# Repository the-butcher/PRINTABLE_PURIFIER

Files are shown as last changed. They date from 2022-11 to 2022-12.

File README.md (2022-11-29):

# PRINTABLE PURIFIER

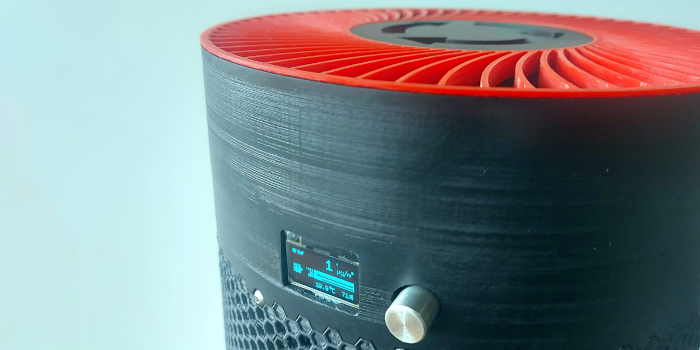
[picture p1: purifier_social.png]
PRINTABLE PURIFIER


An arduino powered air purifier, created mostly from 3D printed parts. Measured PM 2.5 dust readings and other parameters control the purifier's power output.

## [BUILDING INSTRUCTIONS](https://github.com/the-butcher/PRINTABLE_PURIFIER/tree/master/building_instructions/README.md)

Building instructions for the purifier. If you have a 3D-printer that can print 205x205mm you are good to go. I printed mine on an entry level Ancubic Mega S.

## [PART DETAILS](https://github.com/the-butcher/PRINTABLE_PURIFIER/tree/master/unit_purifier)

Complete set of parts provided as STL-Files.

## PICTURES

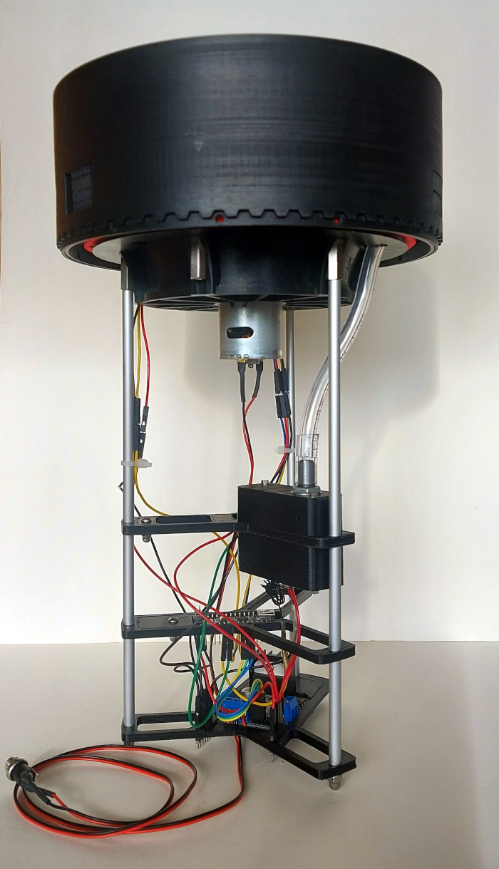
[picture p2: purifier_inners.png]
Purifier


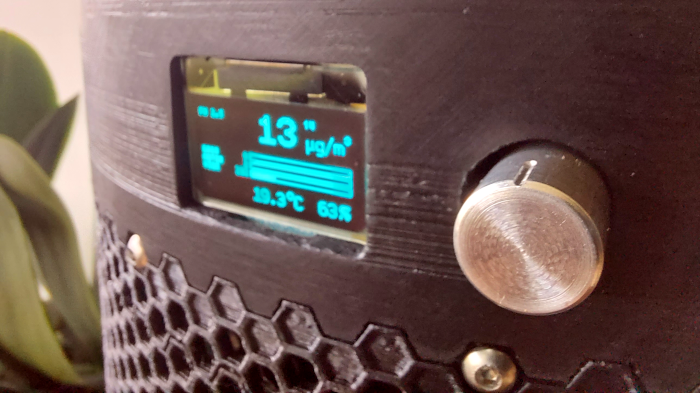
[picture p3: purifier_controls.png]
Purifier


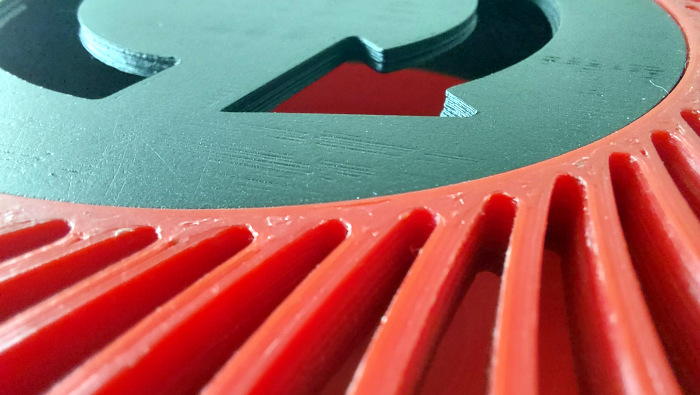
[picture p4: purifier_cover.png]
Purifier


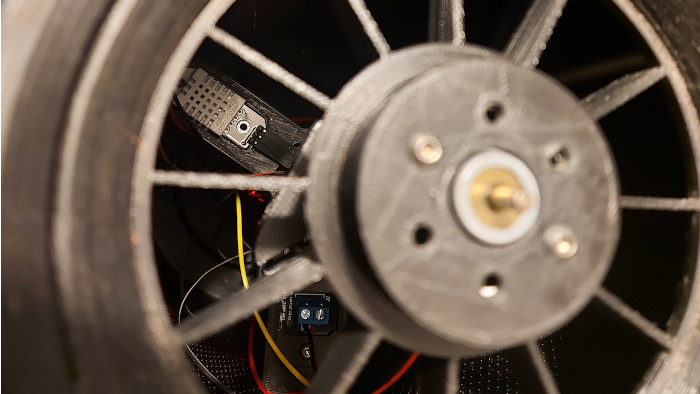
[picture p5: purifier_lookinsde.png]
Purifier


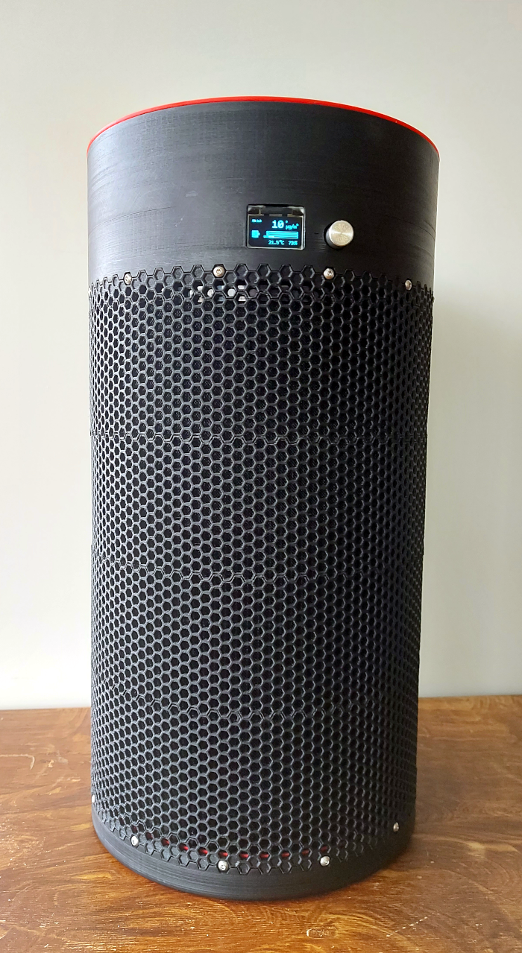
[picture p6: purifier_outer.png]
Purifier


To illustrate power of the device, i placed it upside down and let it run at full power. It actually starts to float on it's own airstream.

https://user-images.githubusercontent.com/84620977/204545599-40bb85f1-9fbe-4fc3-a840-4cbf5077d821.mov

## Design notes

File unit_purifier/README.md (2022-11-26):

# Printable Purifier (unit_purifier)

| | |
| --- | --- |
| Description | Assembly of all parts needed to build the purifier.  |
| Postprocessing | Please refer to postprocessing information of the respective parts. |
| Type | assembly |

---
## [Impeller (unit_impeller)](https://github.com/the-butcher/PRINTABLE_PURIFIER/tree/master/unit_purifier/unit_impeller)

| | |
| --- | --- |
| Description | The impeller is a challenging part to build. It requires precise axis alingnment of your printer and patience to find impeller balance. Please step into folder to find printable STL files.  Please step into folder to find more details and printable STL Files. |
| Type | assembly |

---
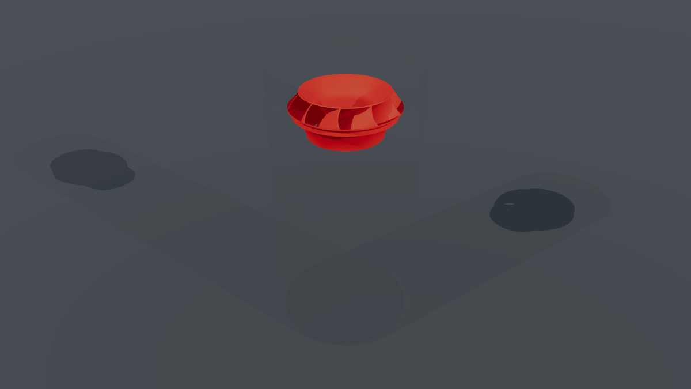
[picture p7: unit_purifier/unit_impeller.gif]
unit_impeller


---

## [Purifier inners (unit_inner)](https://github.com/the-butcher/PRINTABLE_PURIFIER/tree/master/unit_purifier/unit_inner)

| | |
| --- | --- |
| Description | The purifiers electronics were placed to inside the the filter. This part assembles motor, sensors, an arduino nano and the motor driver.  Please step into folder to find more details and printable STL Files. |
| Type | assembly |

---
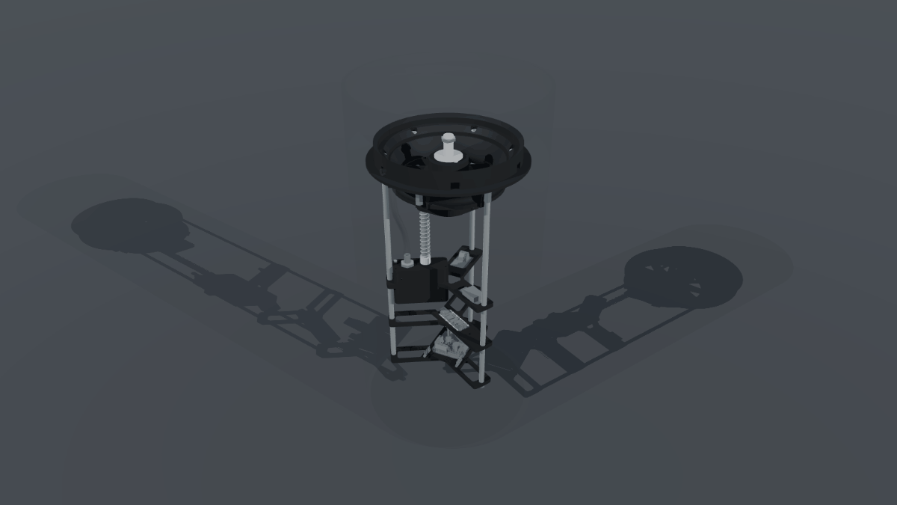
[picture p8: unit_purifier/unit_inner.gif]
unit_inner


---

## [Head (unit_head)](https://github.com/the-butcher/PRINTABLE_PURIFIER/tree/master/unit_purifier/unit_head)

| | |
| --- | --- |
| Description | The purifiers head with display and simple controls.  Please step into folder to find more details and printable STL Files. |
| Postprocessing | Glue "Lower head" to "Upper head", sand the combined part after glue has dried to remove glue remains, spray paint for a better finish. |
| Improvements | When sliding the head over the hub, it does not auto center on the hub. This can lead to not enough space between the impeller and the head. I inserted 6 strips cut from a plastic bottle between head and hub for even spacing. |
| Type | assembly |

---
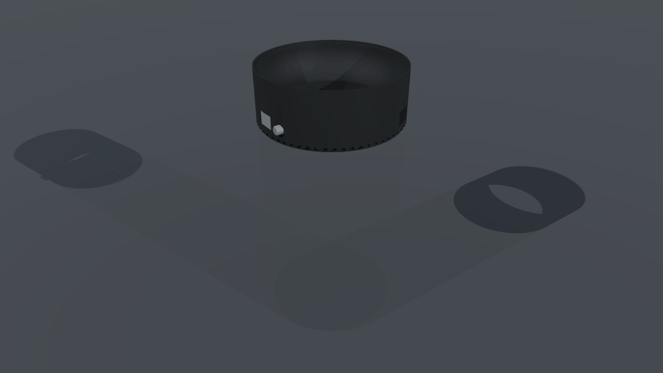
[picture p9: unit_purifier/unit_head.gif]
unit_head


---

## [Housing (unit_honeycomb)](https://github.com/the-butcher/PRINTABLE_PURIFIER/tree/master/unit_purifier/unit_honeycomb)

| | |
| --- | --- |
| Description | Housing around the Xiami Hepa filter.  Please step into folder to find more details and printable STL Files. |
| Type | assembly |

---
unit_honeycomb

---

## [Foot (unit_foot)](https://github.com/the-butcher/PRINTABLE_PURIFIER/tree/master/unit_purifier/unit_foot)

| | |
| --- | --- |
| Description | The purifiers foot.  Please step into folder to find more details and printable STL Files. |
| Type | assembly |

---
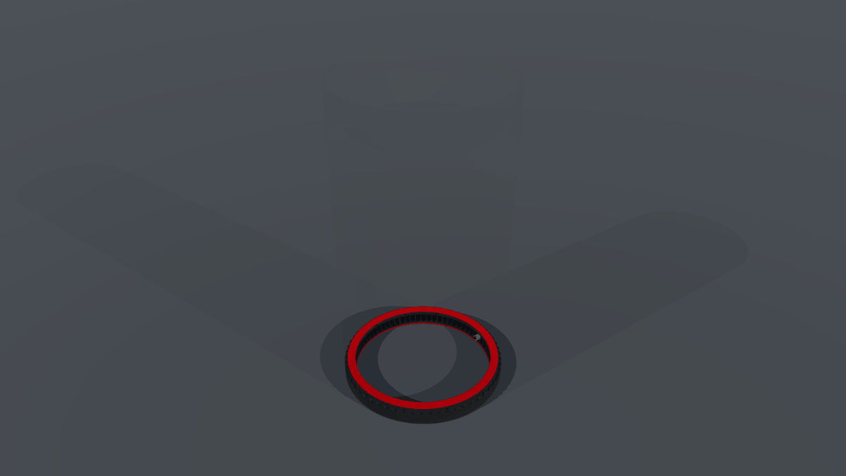
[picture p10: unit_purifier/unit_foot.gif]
unit_foot


---

## [Air outlet (unit_cover)](https://github.com/the-butcher/PRINTABLE_PURIFIER/tree/master/unit_purifier/unit_cover)

| | |
| --- | --- |
| Description | Air outlet assembly.  Please step into folder to find more details and printable STL Files. |
| Type | assembly |

---
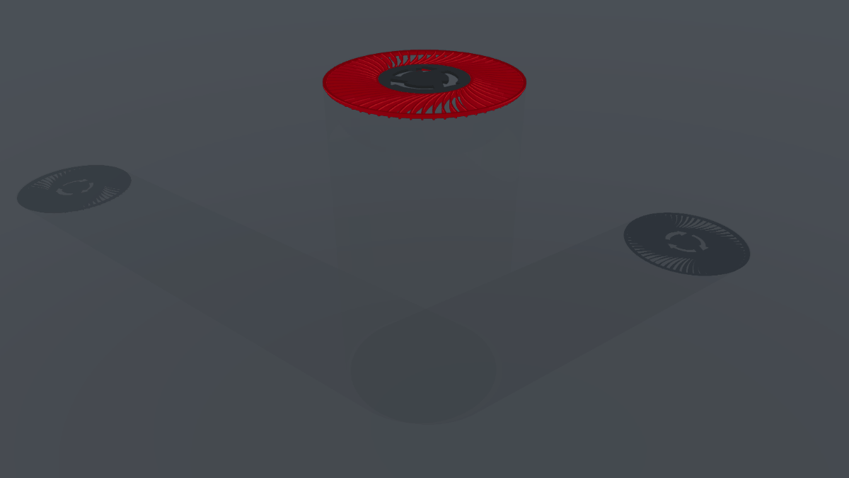
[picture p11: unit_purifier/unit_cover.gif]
unit_cover


---

## [Filter (unit_filter)](https://github.com/the-butcher/PRINTABLE_PURIFIER/tree/master/unit_purifier/unit_filter)

| | |
| --- | --- |
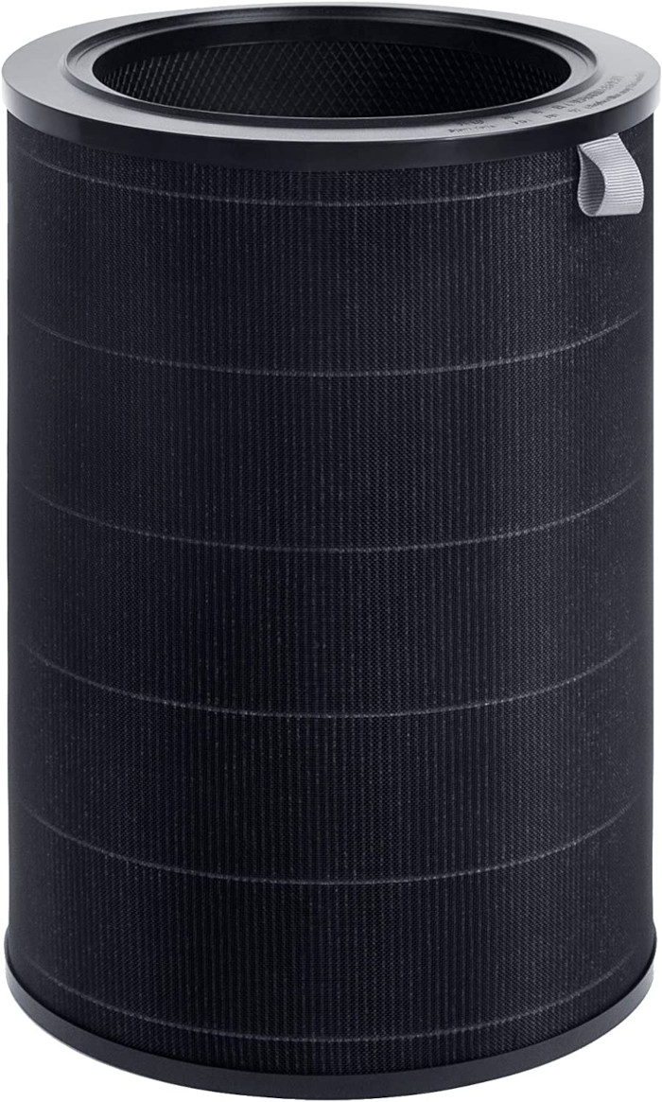
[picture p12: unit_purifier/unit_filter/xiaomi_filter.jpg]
Xiaomi Filter
| Description | The purifier is built around a Xiaomi Smartmi replacement filter. Please search for "Smartmi SMARTMI AIR PURIFIER Activated Carbon Filter, HEPA-H13" and make sure the filter found has the correct product dimensions of 20 x 20 x 29.3 cm.   Please step into folder to find more details and printable STL Files. |
| Type | assembly |

---
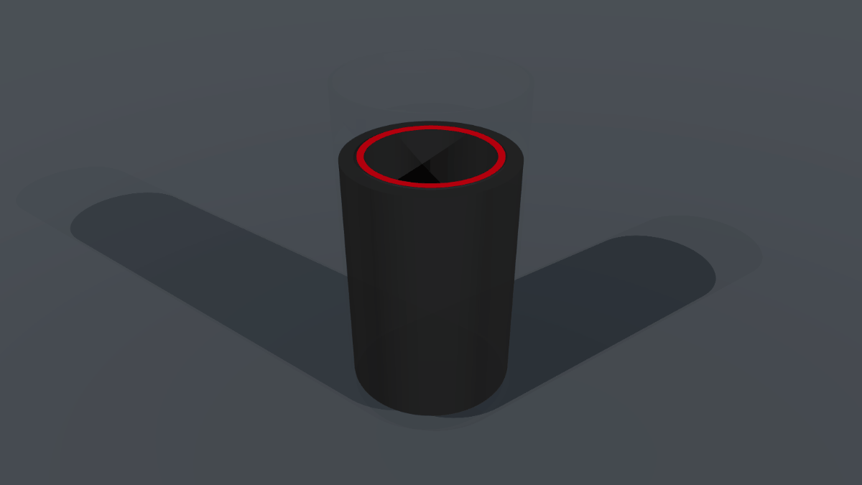
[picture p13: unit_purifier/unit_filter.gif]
unit_filter


---

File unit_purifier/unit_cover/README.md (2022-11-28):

# Air outlet (unit_cover)

| | |
| --- | --- |
| Description | Air outlet assembly.  |
| Type | assembly |

---
## Impeller cover (print_cover_1) &rarr; [STL File](https://github.com/the-butcher/PRINTABLE_PURIFIER/blob/master/unit_purifier/unit_cover/print_cover_1.stl)

| | |
| --- | --- |
| Description | This is the cover plate protecting both your fingers and the impeller.  |
| Improvements | In my build there was not enough space to let the cover slide in, so i had to file down ca. 1mm. I would suggest printing this part after completing the purifier head, so you already know how much space remains to fit it in. |
| Type | 3D print |

---
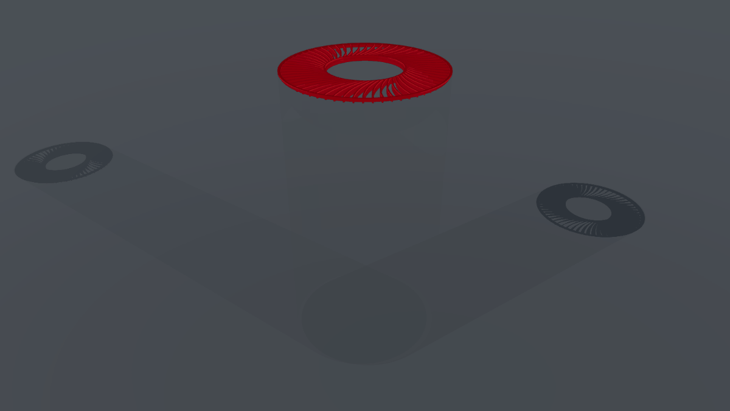
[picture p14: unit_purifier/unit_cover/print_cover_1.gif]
print_cover_1


---

## Customizeable cover (print_cover_2) &rarr; [STL File](https://github.com/the-butcher/PRINTABLE_PURIFIER/blob/master/unit_purifier/unit_cover/print_cover_2.stl)

| | |
| --- | --- |
| Description | This part is meant to be customizable by anyone building this device to give it a personal touch. When creating your own version, please ensure that there are no holes large enough to clear i.e. a child's hand.  |
| Postprocessing | Sand and spray paint for better finish. |
| Type | 3D print |

---
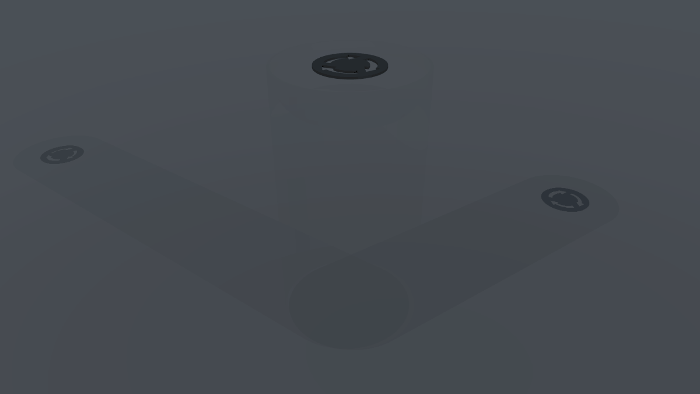
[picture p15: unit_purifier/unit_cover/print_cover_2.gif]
print_cover_2


---

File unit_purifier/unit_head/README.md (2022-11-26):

# Head (unit_head)

| | |
| --- | --- |
| Description | The purifiers head with display and simple controls.  |
| Postprocessing | Glue "Lower head" to "Upper head", sand the combined part after glue has dried to remove glue remains, spray paint for a better finish. |
| Improvements | When sliding the head over the hub, it does not auto center on the hub. This can lead to not enough space between the impeller and the head. I inserted 6 strips cut from a plastic bottle between head and hub for even spacing. |
| Type | assembly |

---
## Head connector (print_outer_connect) &rarr; [STL File](https://github.com/the-butcher/PRINTABLE_PURIFIER/blob/master/unit_purifier/unit_head/print_outer_connect.stl)

| | |
| --- | --- |
| Description | This part connects the outer and inner parts of the head.  |
| Postprocessing | With a 3mm drill widen the 12 holes. This will make it easier to insert the M3 screws when assembling the purifier. |
| Type | 3D print |

---
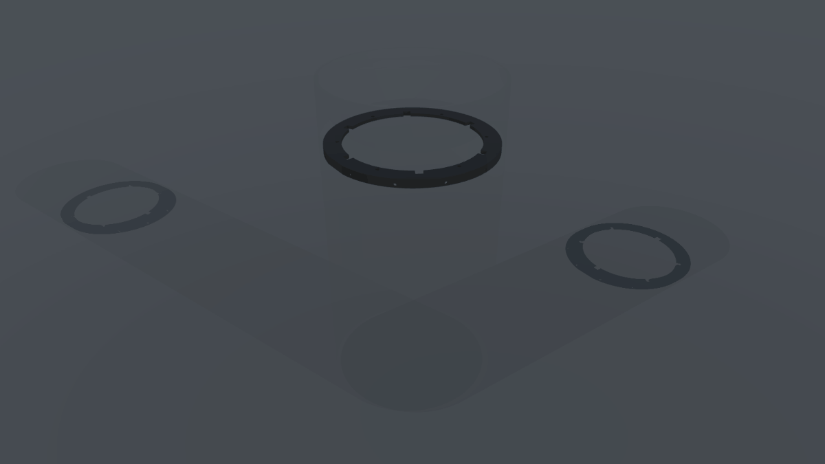
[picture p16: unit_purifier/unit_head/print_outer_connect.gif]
print_outer_connect


---

## Lower head (print_outer_controls) &rarr; [STL File](https://github.com/the-butcher/PRINTABLE_PURIFIER/blob/master/unit_purifier/unit_head/print_outer_controls.stl)

| | |
| --- | --- |
| Description | The lower part of the outfacing head. This part holds the OLED display and the potentiometer that controls the power setting.  |
| Postprocessing | User pliers to remove supports. Clean up openings for display and potentiometer so these fit properly. |
| Improvements | In my build the pins on the outside of the OLED display were portruding too far to fit the display. I had to file away some material from the display opening. |
| Type | 3D print |

---
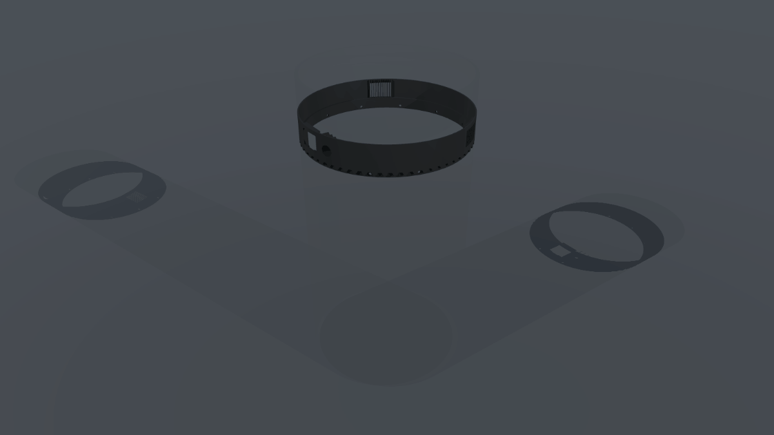
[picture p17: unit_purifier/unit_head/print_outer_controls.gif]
print_outer_controls


---

## Inner head (print_outer_outlet) &rarr; [STL File](https://github.com/the-butcher/PRINTABLE_PURIFIER/blob/master/unit_purifier/unit_head/print_outer_outlet.stl)

| | |
| --- | --- |
| Description | The infacing part of the head.  |
| Postprocessing | Use a 4mm drill to open the screwholes. Use a 4mm screw to pull M4 nuts into the respective openings. The nuts should have a tight fit and not come out, once seated.
Sand and spray for a better finish. |
| Type | 3D print |

---
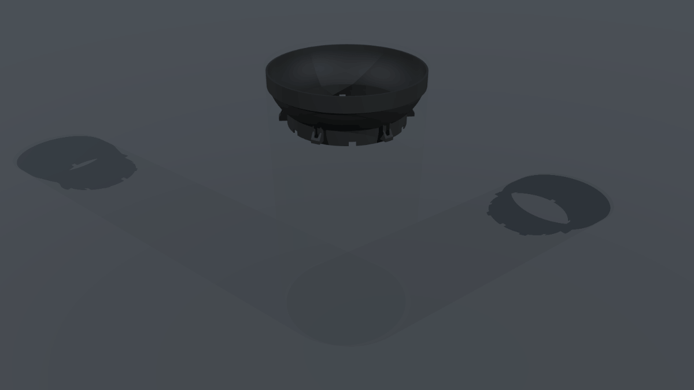
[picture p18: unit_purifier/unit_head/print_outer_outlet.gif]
print_outer_outlet


---

## Upper head (print_outer_ring) &rarr; [STL File](https://github.com/the-butcher/PRINTABLE_PURIFIER/blob/master/unit_purifier/unit_head/print_outer_ring.stl)

| | |
| --- | --- |
| Description | The upper part of the outfacing head.  |
| Type | 3D print |

---
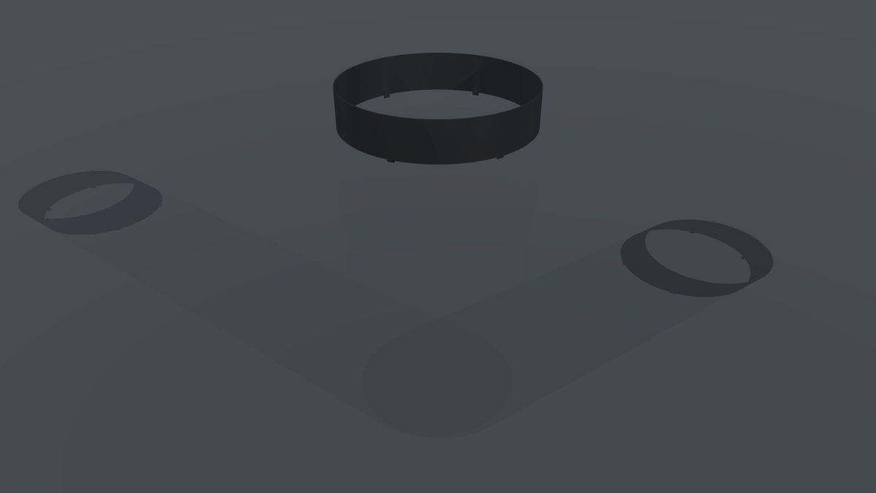
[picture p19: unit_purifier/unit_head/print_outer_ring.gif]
print_outer_ring


---

## Display (display_ssd1306)

| | |
| --- | --- |
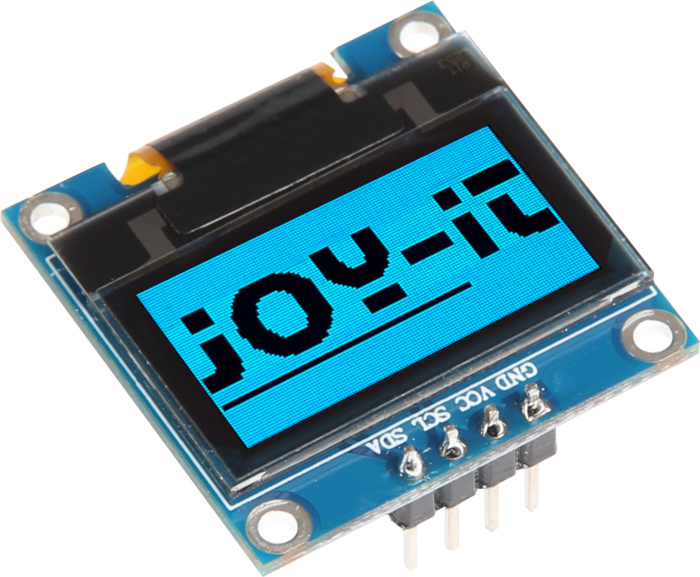
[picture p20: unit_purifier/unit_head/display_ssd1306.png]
SD1306
| Description | Type SSD1306 display. Search the internet for SD1306 display.   |
| Type | electronic |

---

## Potentiometer (poti_smc10h04103)

| | |
| --- | --- |
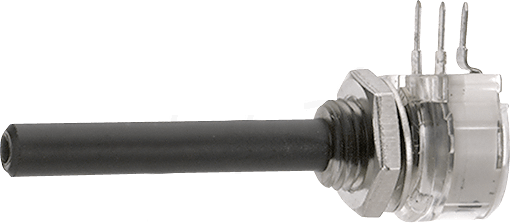
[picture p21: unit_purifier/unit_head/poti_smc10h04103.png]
smc10h04103
| Description | Ptentiometer 10 kOhm. Search the internet for poti_smc10h04103 potentiometer.   |
| Type | electronic |

---

## M4 nut (hardware_nut_m4)

| | |
| --- | --- |
| Description | M4 nut, 6 pieces.  |
| Type | hardware |

---

## M4 screw (hardware_allen_m4_14mm)

| | |
| --- | --- |
| Description | M4 allen screw, 14mm long. 6 pieces.  |
| Type | hardware |

---

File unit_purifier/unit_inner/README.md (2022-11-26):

# Purifier inners (unit_inner)

| | |
| --- | --- |
| Description | The purifiers electronics were placed to inside the the filter. This part assembles motor, sensors, an arduino nano and the motor driver.  |
| Type | assembly |

---
## [Hub (unit_hub)](https://github.com/the-butcher/PRINTABLE_PURIFIER/tree/master/unit_purifier/unit_inner/unit_hub)

| | |
| --- | --- |
| Description | The hub holds the motor and acts a guide for the air as it exits the filter.  Please step into folder to find more details and printable STL Files. |
| Type | assembly |

---
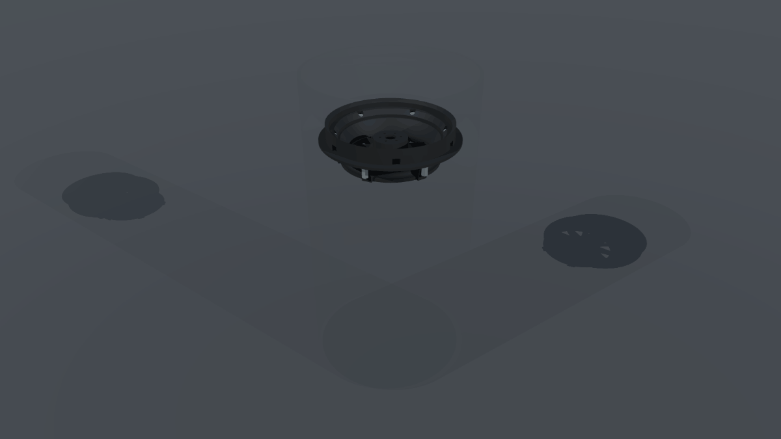
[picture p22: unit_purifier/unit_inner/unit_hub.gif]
unit_hub


---

## [Motor assembly (unit_motor)](https://github.com/the-butcher/PRINTABLE_PURIFIER/tree/master/unit_purifier/unit_inner/unit_motor)

| | |
| --- | --- |
| Description | The motor assembly contains the motor, the connecting part to the impeller and a connection to the vibration sensor.  Please step into folder to find more details and printable STL Files. |
| Type | assembly |

---
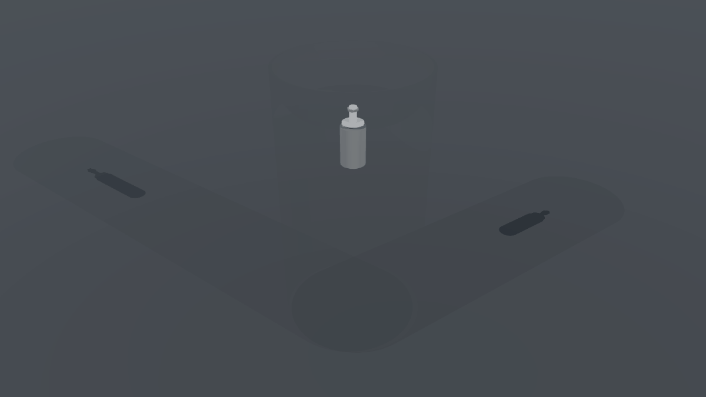
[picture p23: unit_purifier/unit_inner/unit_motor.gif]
unit_motor


---

## [Arduino Nano (unit_nano)](https://github.com/the-butcher/PRINTABLE_PURIFIER/tree/master/unit_purifier/unit_inner/unit_nano)

| | |
| --- | --- |
| Description | The plate holding the Arduino Nano.  Please step into folder to find more details and printable STL Files. |
| Type | assembly |

---
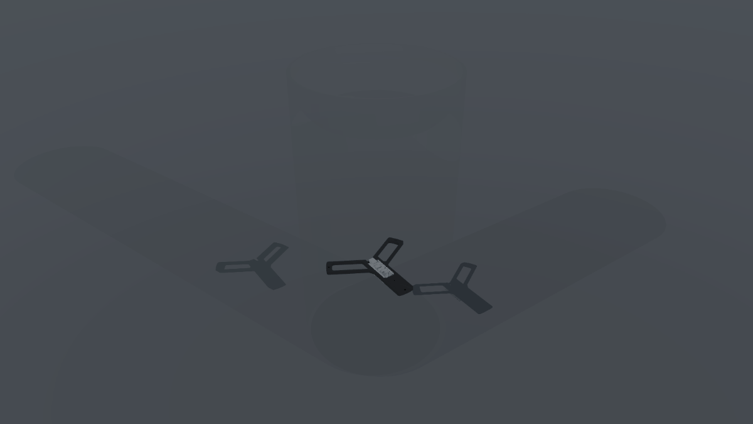
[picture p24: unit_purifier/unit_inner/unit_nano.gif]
unit_nano


---

## [Motor driver (unit_power)](https://github.com/the-butcher/PRINTABLE_PURIFIER/tree/master/unit_purifier/unit_inner/unit_power)

| | |
| --- | --- |
| Description | The plate holding the L298N motor driver.  Please step into folder to find more details and printable STL Files. |
| Type | assembly |

---
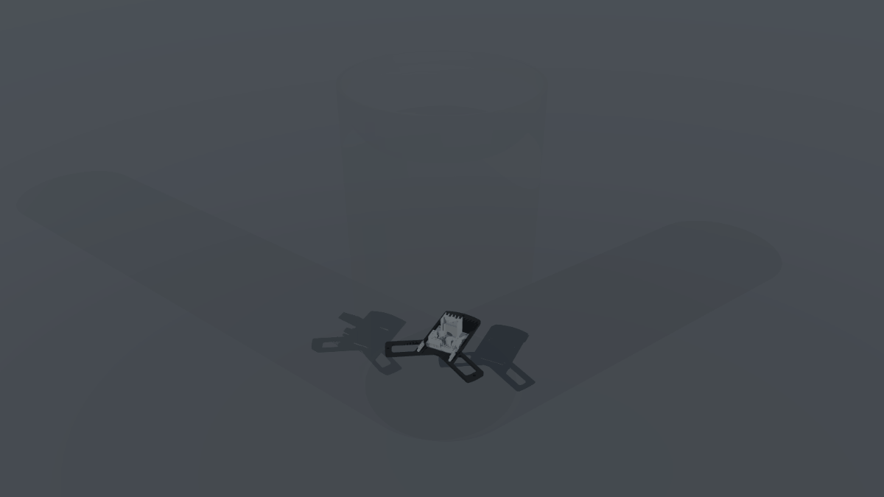
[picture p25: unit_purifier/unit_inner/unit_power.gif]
unit_power


---

## [Sensors (unit_sensors)](https://github.com/the-butcher/PRINTABLE_PURIFIER/tree/master/unit_purifier/unit_inner/unit_sensors)

| | |
| --- | --- |
| Description | The plate holding the sensors.  Please step into folder to find more details and printable STL Files. |
| Type | assembly |

---
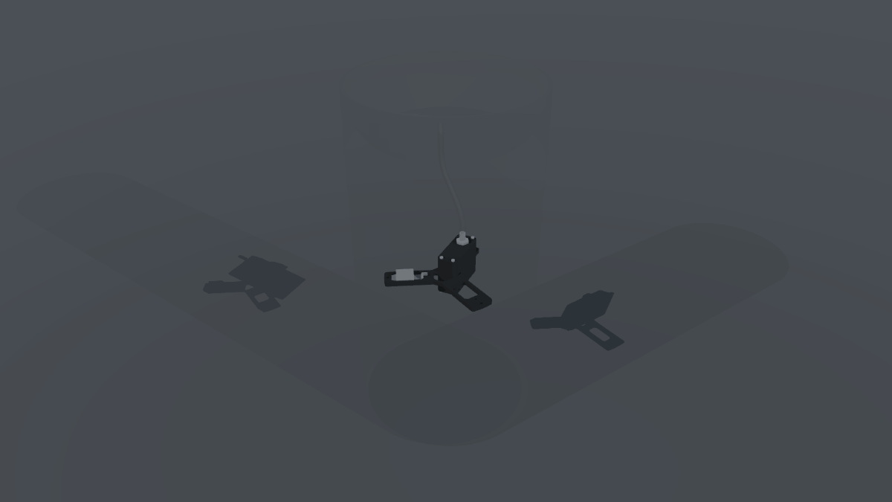
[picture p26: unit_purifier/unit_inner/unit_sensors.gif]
unit_sensors


---

## [Screws (unit_screws)](https://github.com/the-butcher/PRINTABLE_PURIFIER/tree/master/unit_purifier/unit_inner/unit_screws)

| | |
| --- | --- |
| Description | All hardware needed to assemble the purifier inner parts.  Please step into folder to find more details and printable STL Files. |
| Type | assembly |

---
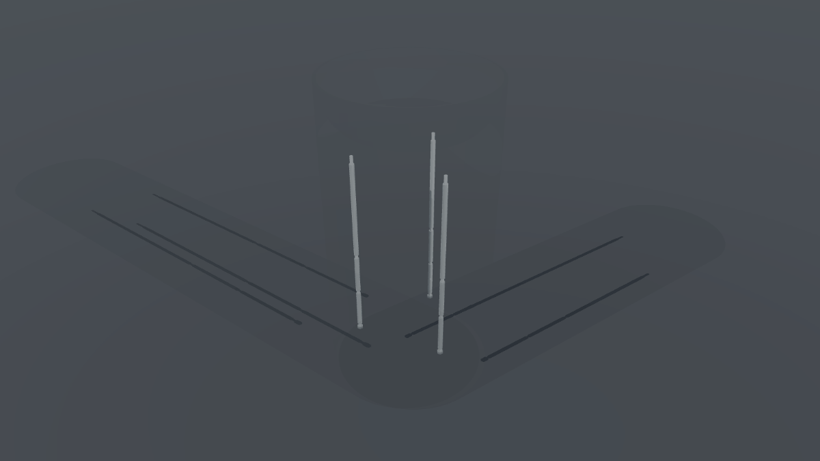
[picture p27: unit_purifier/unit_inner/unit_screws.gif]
unit_screws


---

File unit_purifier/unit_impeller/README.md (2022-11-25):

# Impeller (unit_impeller)

| | |
| --- | --- |
| Description | The impeller is a challenging part to build. It requires precise axis alingnment of your printer and patience to find impeller balance. Please step into folder to find printable STL files.  |
| Type | assembly |

---
## Lower impeller (print_impeller_1) &rarr; [STL File](https://github.com/the-butcher/PRINTABLE_PURIFIER/blob/master/unit_purifier/unit_impeller/print_impeller_1.stl)

| | |
| --- | --- |
| Description | The lower part of the impeller.  |
| Type | 3D print |

---
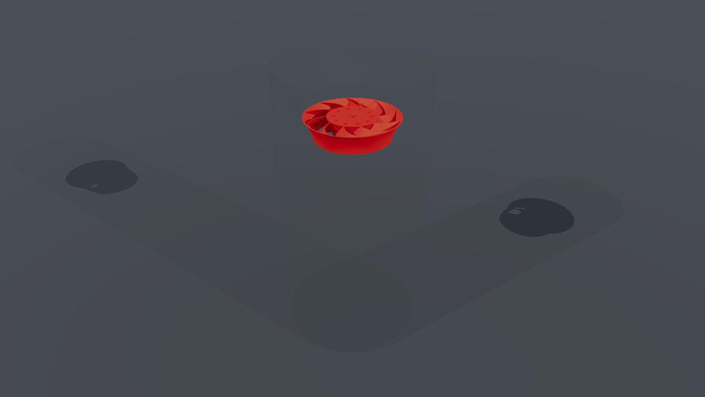
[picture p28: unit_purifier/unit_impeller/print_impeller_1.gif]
print_impeller_1


---

## Upper Impeller (print_impeller_2) &rarr; [STL File](https://github.com/the-butcher/PRINTABLE_PURIFIER/blob/master/unit_purifier/unit_impeller/print_impeller_2.stl)

| | |
| --- | --- |
| Description | The upper part of the impeller.  |
| Type | 3D print |

---
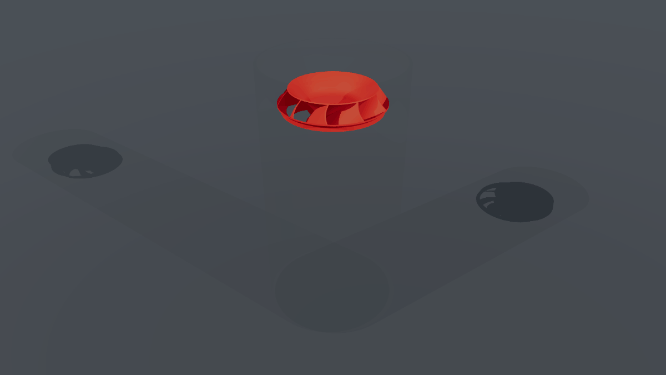
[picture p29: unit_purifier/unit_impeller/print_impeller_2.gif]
print_impeller_2


---

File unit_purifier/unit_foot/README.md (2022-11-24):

# Foot (unit_foot)

| | |
| --- | --- |
| Description | The purifiers foot.  |
| Type | assembly |

---
## Foot (print_outer_foot) &rarr; [STL File](https://github.com/the-butcher/PRINTABLE_PURIFIER/blob/master/unit_purifier/unit_foot/print_outer_foot.stl)

| | |
| --- | --- |
| Description | The purifiers foot  |
| Postprocessing | User pliers to remove supports from plug opening and cut M8x1 fine thread to fit the power plug. Sand and spray paint for a better finish. Cut rings of foam rubber for both bottom and top of the foot, then glue foam rubber to foot. |
| Type | 3D print |

---
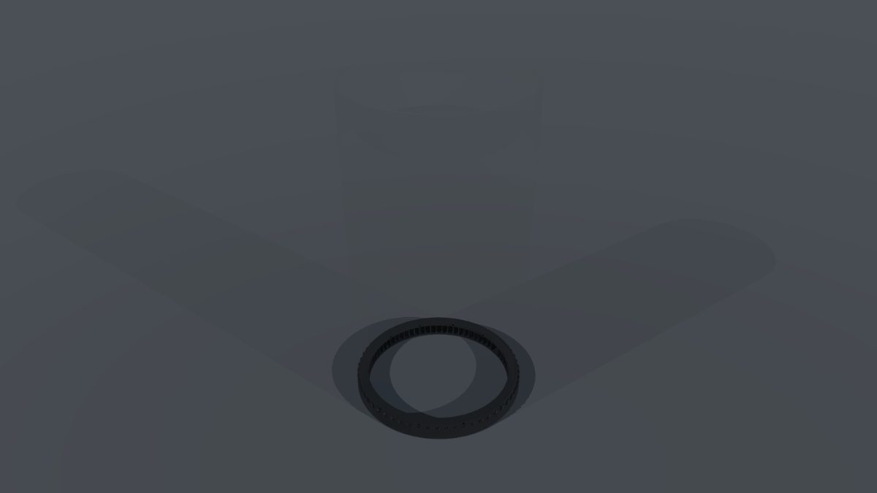
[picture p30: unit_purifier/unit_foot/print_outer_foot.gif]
print_outer_foot


---

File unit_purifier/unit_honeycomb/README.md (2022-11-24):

# Housing (unit_honeycomb)

| | |
| --- | --- |
| Description | Housing around the Xiami Hepa filter.  |
| Type | assembly |

---
## Lower housing (print_honeycomb_1) &rarr; [STL File](https://github.com/the-butcher/PRINTABLE_PURIFIER/blob/master/unit_purifier/unit_honeycomb/print_honeycomb_1.stl)

| | |
| --- | --- |
| Description | The lower border of the purifier housing.  |
| Postprocessing | User pliers to remove supports. Carefully widen the 1mm holes to 2mm first, then to 3mm. File and sand the upper hexagon border so it properly fits the upper housing part. I used rough sand paper wrapped around an allen key to file multiple hexagon side at once. |
| Type | 3D print |

---
print_honeycomb_1

---

## Center housing (print_honeycomb_2) &rarr; [STL File](https://github.com/the-butcher/PRINTABLE_PURIFIER/blob/master/unit_purifier/unit_honeycomb/print_honeycomb_2.stl)

| | |
| --- | --- |
| Description | The center piece of the purifier housing. Attention: 4 pieces needed to get the full housing.  |
| Postprocessing | User pliers to remove supports. File and sand upper and lower hexagon border so it properly fits the housing parts above and below. I used rough sand paper wrapped around an allen key to file multiple hexagon side at once. |
| Type | 3D print |

---
print_honeycomb_2

---

## Upper housing (print_honeycomb_3) &rarr; [STL File](https://github.com/the-butcher/PRINTABLE_PURIFIER/blob/master/unit_purifier/unit_honeycomb/print_honeycomb_3.stl)

| | |
| --- | --- |
| Description | The upper border of the purifier housing.  |
| Postprocessing | User pliers to remove supports. Carefully widen the 1mm holes to 2mm first, then to 3mm. File and sand the lower hexagon border so it properly fits the housing part below. I used rough sand paper wrapped around an allen key to file multiple hexagon side at once. |
| Type | 3D print |

---
print_honeycomb_3

---

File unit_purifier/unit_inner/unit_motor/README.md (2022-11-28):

# Motor assembly (unit_motor)

| | |
| --- | --- |
| Description | The motor assembly contains the motor, the connecting part to the impeller and a connection to the vibration sensor.  |
| Type | assembly |

---
## Impeller mount (lathe_motor_connect) &rarr; [STL File](https://github.com/the-butcher/PRINTABLE_PURIFIER/blob/master/unit_purifier/unit_inner/unit_motor/lathe_motor_connect.stl)

| | |
| --- | --- |
| Description | This part is used to connect the impeller parts and to fix the impeller to the 3.2mm axle of the motor. In my build i made the part from a leftover piece of 30mm POM  |
| Postprocessing | Cut a M10x1 thread on the 10mm end of the part, use a M10x1 nut for connecting the impeller parts. Have a 3mm hole in the part for a firm fit when pushing the part onto the motor axle. |
| Type | lathe |

---

## Motor (motor_555_1)

| | |
| --- | --- |
| Description | Type 555-1 motor. Search the internet for 555-1 motor.   |
| Type | electronic |

---

## M3 lens head (hardware_flat_allen_m3)

| | |
| --- | --- |
| Description | M3 lens head allen screw, 10mm long, 2 pieces.  |
| Type | hardware |

---

## M10x1 nut (hardware_nut_m10)

| | |
| --- | --- |
| Description | M10x1 fine threaded nut.  |
| Type | hardware |

---

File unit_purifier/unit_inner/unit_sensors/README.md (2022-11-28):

# Sensors (unit_sensors)

| | |
| --- | --- |
| Description | The plate holding the sensors.  |
| Type | assembly |

---
## Sensor Plate (print_holder_sensors_1) &rarr; [STL File](https://github.com/the-butcher/PRINTABLE_PURIFIER/blob/master/unit_purifier/unit_inner/unit_sensors/print_holder_sensors_1.stl)

| | |
| --- | --- |
| Description | The main plate holding Dust, Temperature and Vibration Sensor.  |
| Type | 3D print |

---
print_holder_sensors_1

---

## Sensor holder (print_holder_sensors_2) &rarr; [STL File](https://github.com/the-butcher/PRINTABLE_PURIFIER/blob/master/unit_purifier/unit_inner/unit_sensors/print_holder_sensors_2.stl)

| | |
| --- | --- |
| Description | Holding plate for the Vibration sensor.  |
| Type | 3D print |

---
print_holder_sensors_2

---

## Sensor housing (print_holder_sensors_3) &rarr; [STL File](https://github.com/the-butcher/PRINTABLE_PURIFIER/blob/master/unit_purifier/unit_inner/unit_sensors/print_holder_sensors_3.stl)

| | |
| --- | --- |
| Description | Upper housing of the dust sensor.  |
| Type | 3D print |

---
print_holder_sensors_3

---

## Sensor housing (print_holder_sensors_4) &rarr; [STL File](https://github.com/the-butcher/PRINTABLE_PURIFIER/blob/master/unit_purifier/unit_inner/unit_sensors/print_holder_sensors_4.stl)

| | |
| --- | --- |
| Description | Lower housing of the dust sensor.  |
| Type | 3D print |

---
print_holder_sensors_4

---

## Dust sensor (sensor_pd_m4)

| | |
| --- | --- |
| Description | The dust sensor is the input to the purifiers power level, together with the potentiometer setting. I used a sensor that i already had: PD-M4 [PM-D4](http://www.csfan.co.kr/bbs/board.php?bo_table=products1&wr_id=15&ckattempt=2). This sensor appears not to be available in retail, therefore another sensor may have to be used, thus requiring changes to the sensor plate and to the sensor housing parts!  |
| Type | electronic |

---

## Temperature and humidity sensor (sensor_dht22)

| | |
| --- | --- |
| Description | For added value a temperature and humidity sensor was included. This sensor provided information only and does not contribute to the purifiers power setting. Sensor used: DHT22 [DHT22](https://joy-it.net/en/products/SEN-DHT22)  |
| Type | electronic |

---

## M2 rod (hardware_rod_m2_49)

| | |
| --- | --- |
| Description | M2 rod, 49mm long, 4 pieces.  |
| Type | hardware |

---

## M12 nut (hardware_nut_m2)

| | |
| --- | --- |
| Description | M2 nut. 8 pieces.  |
| Type | hardware |

---

## M10x1 nut (hardware_nut_m10)

| | |
| --- | --- |
| Description | M10x1 fine threaded nut. 2 pieces.  |
| Type | hardware |

---

## Cleartube (hardware_cleartube_10)

| | |
| --- | --- |
| Description | Cleartube, 10mm diameter, ~140mm long.  |
| Type | hardware |

---

## Cleartube (hardware_cleartube_12)

| | |
| --- | --- |
| Description | Cleartube, 12mm diameter, 20mm long.  |
| Type | hardware |

---

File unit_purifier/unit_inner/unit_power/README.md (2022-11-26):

# Motor driver (unit_power)

| | |
| --- | --- |
| Description | The plate holding the L298N motor driver.  |
| Type | assembly |

---
## Driver Plate (print_holder_power_1) &rarr; [STL File](https://github.com/the-butcher/PRINTABLE_PURIFIER/blob/master/unit_purifier/unit_inner/unit_power/print_holder_power_1.stl)

| | |
| --- | --- |
| Description | The main plate holding the motor driver.  |
| Type | 3D print |

---
print_holder_power_1

---

## Driver holder (print_holder_power_2) &rarr; [STL File](https://github.com/the-butcher/PRINTABLE_PURIFIER/blob/master/unit_purifier/unit_inner/unit_power/print_holder_power_2.stl)

| | |
| --- | --- |
| Description | Holding plate for the motor driver.  |
| Type | 3D print |

---
print_holder_power_2

---

## Motor driver (driver_l298n)

| | |
| --- | --- |
| Description | The L298N driver regulating motor power. L298N  |
| Type | electronic |

---

## Power plug (driver_plug_5521)

| | |
| --- | --- |
| Description | Power plug 5.5x2.1 mm. Power Plug  |
| Type | electronic |

---

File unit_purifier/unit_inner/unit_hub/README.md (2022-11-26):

# Hub (unit hub)

| | |
| --- | --- |
| Description | The hub holds the motor and acts a guide for the air as it exits the filter.  |
| Type | assembly |

---
## Lower hub (print_hub_1) &rarr; [STL File](https://github.com/the-butcher/PRINTABLE_PURIFIER/blob/master/unit_purifier/unit_inner/unit_hub/print_hub_1.stl)

| | |
| --- | --- |
| Description | The lower part of the impeller hub.  |
| Postprocessing | Remove the supports. Smoothen air outlet a bit to improve air flow and reduce noise. |
| Improvements | Create supports that are easier to remove, especially for the motor opening. Maybe make the motor opening a little larger, i had to do some sanding in my build before the motor could be fitted. |
| Type | 3D print |

---
print_hub_1

---

## Upper hub. (print_hub_2) &rarr; [STL File](https://github.com/the-butcher/PRINTABLE_PURIFIER/blob/master/unit_purifier/unit_inner/unit_hub/print_hub_2.stl)

| | |
| --- | --- |
| Description | The upper part of the impeller hub.  |
| Postprocessing | Remove support from the opening where the dust sensors tub passed through. Later place electric tape over the unused outlet openings. |
| Type | 3D print |

---
print_hub_2

---

## M4 long nut (hardware_nut_m4_20mm)

| | |
| --- | --- |
| Description | M4 nut, 20mm long, 6 pieces.  |
| Type | hardware |

---

## M4 screw (hardware_allen_m4_14mm)

| | |
| --- | --- |
| Description | M4 allen screw, 14mm long. 6 pieces.  |
| Type | hardware |

---

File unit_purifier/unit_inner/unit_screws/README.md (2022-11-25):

# Screws (unit_screws)

| | |
| --- | --- |
| Description | All hardware needed to assemble the purifier inner parts.  |
| Type | assembly |

---
## M4 rod (hardware_rod_m4_253)

| | |
| --- | --- |
| Description | M4 rod, 253mm long, 3 pieces.  |
| Type | hardware |

---

## Aluminum Tube (hardware_tube_6_1_125)

| | |
| --- | --- |
| Description | Aluminum Tube 6x1mm 125mm long, 3 pieces.  |
| Type | hardware |

---

## Aluminum Tube (hardware_tube_6_1_50)

| | |
| --- | --- |
| Description | Aluminum Tube 6x1mm 50mm long, 6 pieces.  |
| Type | hardware |

---

## M4 nut (hardware_nut_m4)

| | |
| --- | --- |
| Description | M4 nut, 3 pieces.  |
| Type | hardware |

---

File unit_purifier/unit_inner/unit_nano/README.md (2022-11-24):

# Arduino Nano (unit_nano)

| | |
| --- | --- |
| Description | The plate holding the Arduino Nano.  |
| Type | assembly |

---
## Controller Plate (print_holder_nano_1) &rarr; [STL File](https://github.com/the-butcher/PRINTABLE_PURIFIER/blob/master/unit_purifier/unit_inner/unit_nano/print_holder_nano_1.stl)

| | |
| --- | --- |
| Description | The main plate holding the Arduino Nano.  |
| Type | 3D print |

---
print_holder_nano_1

---

## Controller holder (print_holder_nano_2) &rarr; [STL File](https://github.com/the-butcher/PRINTABLE_PURIFIER/blob/master/unit_purifier/unit_inner/unit_nano/print_holder_nano_2.stl)

| | |
| --- | --- |
| Description | Holding plate for the Arduino Nano.  |
| Type | 3D print |

---
print_holder_nano_2

---

## Arduino Nano (arduino_nano)

| | |
| --- | --- |
| Description | An original Arduino Nano or a Nano clone.  Arduino Nano  |
| Type | electronic |

---

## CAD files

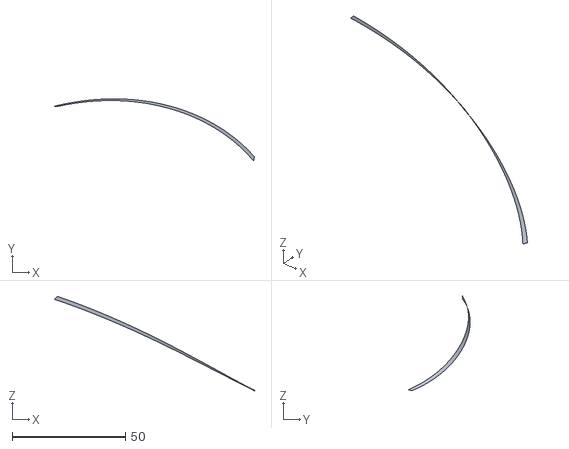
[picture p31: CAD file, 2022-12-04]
misc/imp_test_draw_curve2_wing_sec_b.stl
88.3 x 27.5 x 41.6

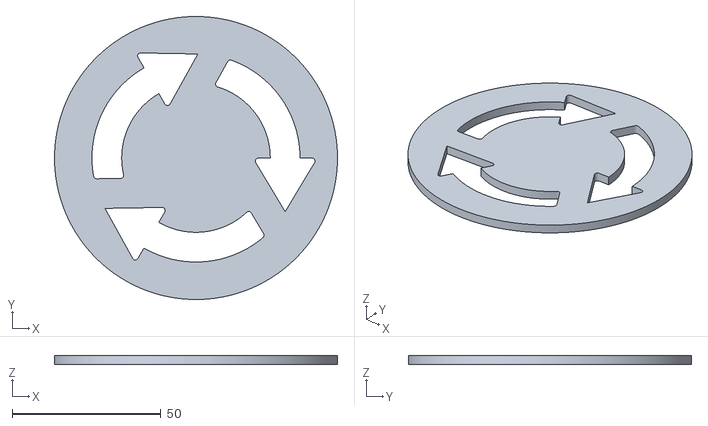
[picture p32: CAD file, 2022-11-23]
unit_purifier/unit_cover/print_cover_2.stl
95.2 x 95.2 x 3.00

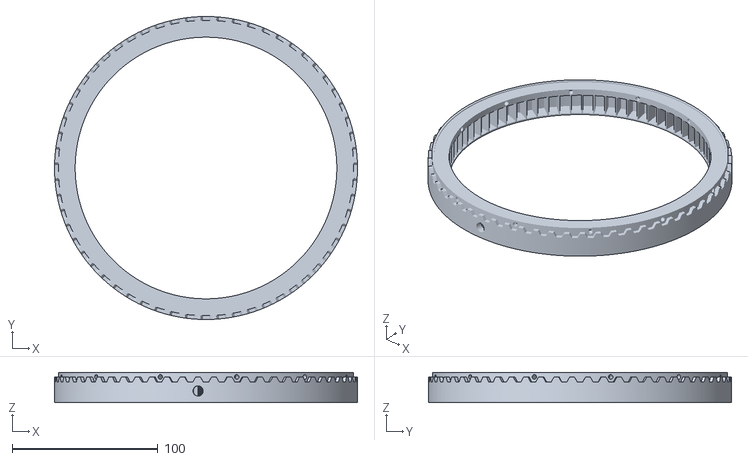
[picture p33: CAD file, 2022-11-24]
unit_purifier/unit_foot/print_outer_foot.stl
208.0 x 208.0 x 20.8

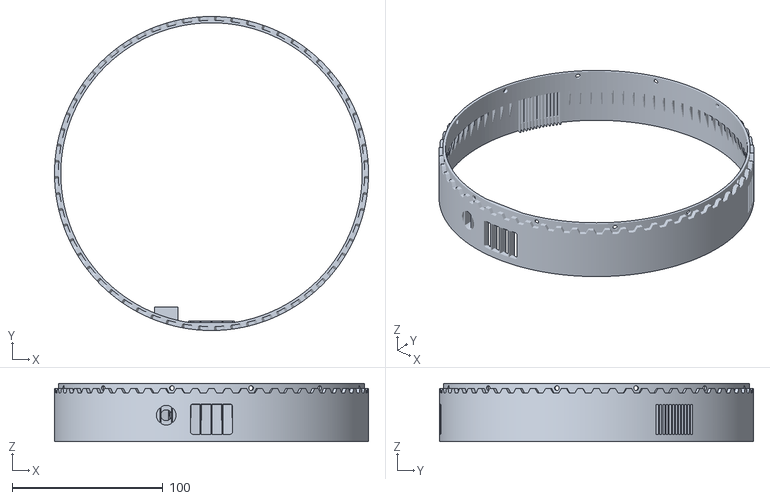
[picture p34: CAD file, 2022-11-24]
unit_purifier/unit_head/print_outer_controls.stl
208.0 x 208.0 x 38.6

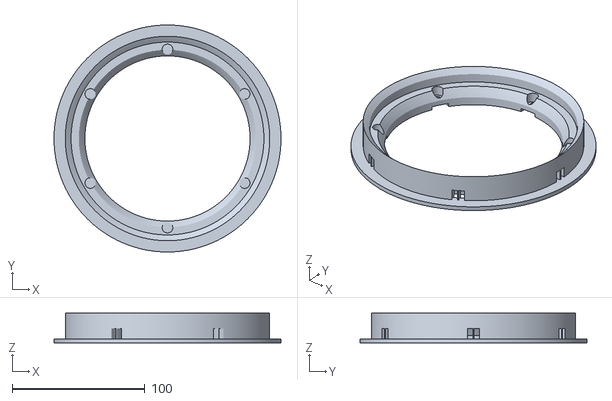
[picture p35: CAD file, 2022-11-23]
unit_purifier/unit_inner/unit_hub/print_hub_2.stl
170.7 x 170.7 x 22.3

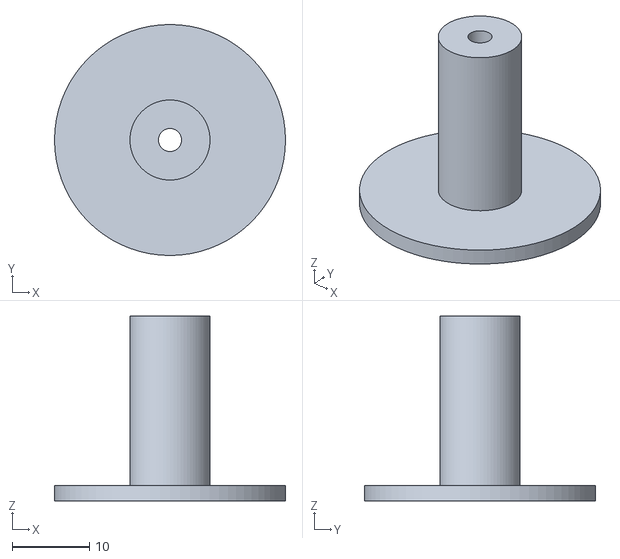
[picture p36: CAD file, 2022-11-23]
unit_purifier/unit_inner/unit_motor/lathe_motor_connect.stl
30.0 x 30.0 x 24.0

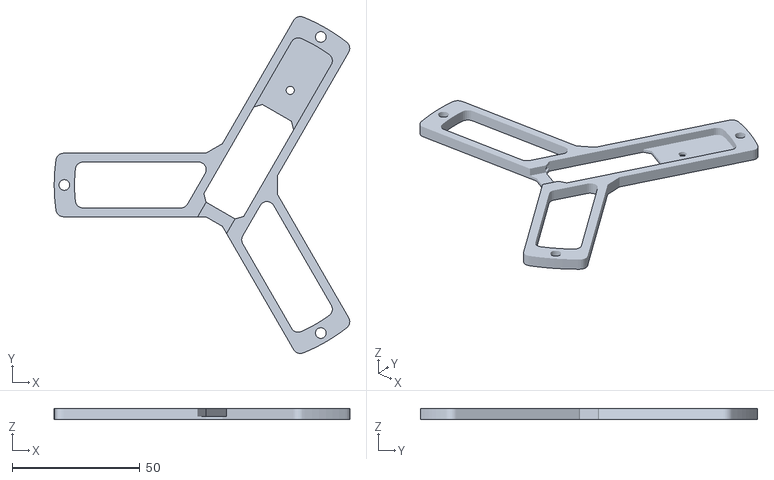
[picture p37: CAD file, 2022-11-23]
unit_purifier/unit_inner/unit_nano/print_holder_nano_1.stl
115.9 x 132.1 x 4.38

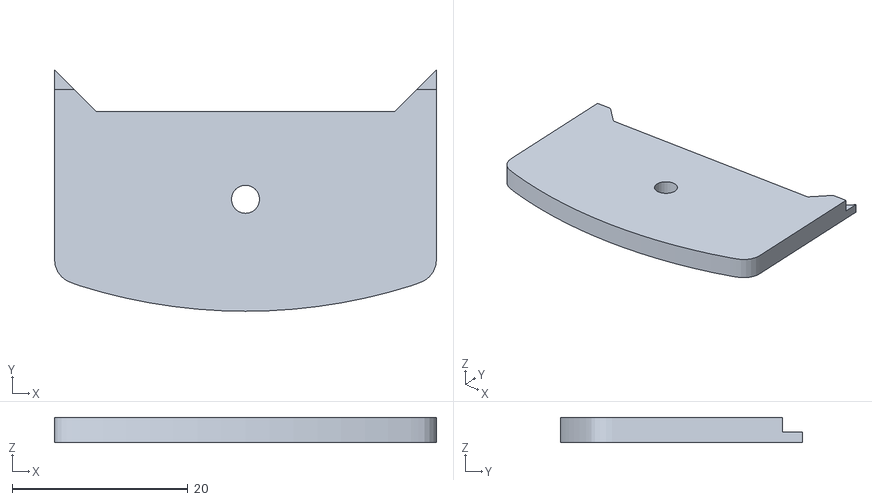
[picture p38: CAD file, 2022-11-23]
unit_purifier/unit_inner/unit_power/print_holder_power_2.stl
43.5 x 27.5 x 2.90

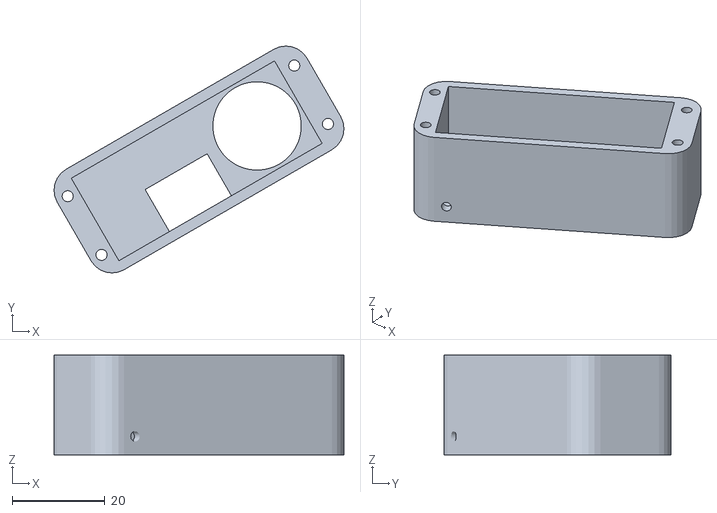
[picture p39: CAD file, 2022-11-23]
unit_purifier/unit_inner/unit_sensors/print_holder_sensors_4.stl
62.4 x 48.8 x 21.4

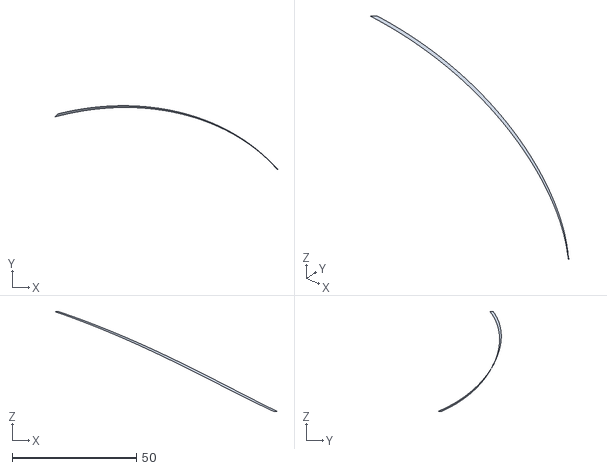
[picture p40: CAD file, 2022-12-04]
misc/imp_test_draw_curve2_wing_sec_c.stl
89.8 x 25.6 x 40.3

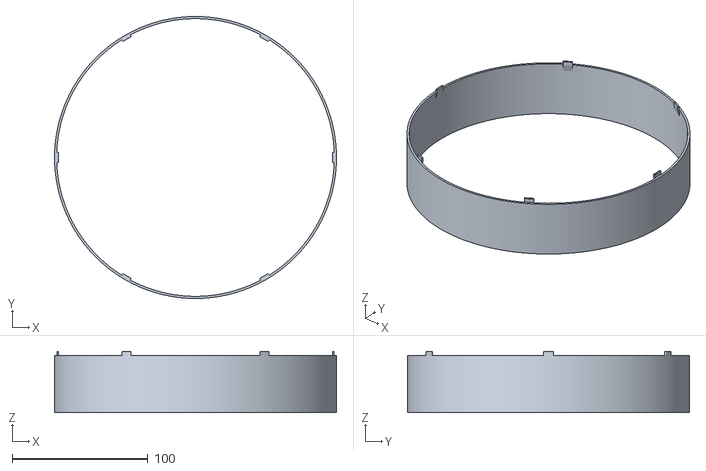
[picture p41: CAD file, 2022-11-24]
unit_purifier/unit_head/print_outer_ring.stl
208.0 x 208.0 x 45.2

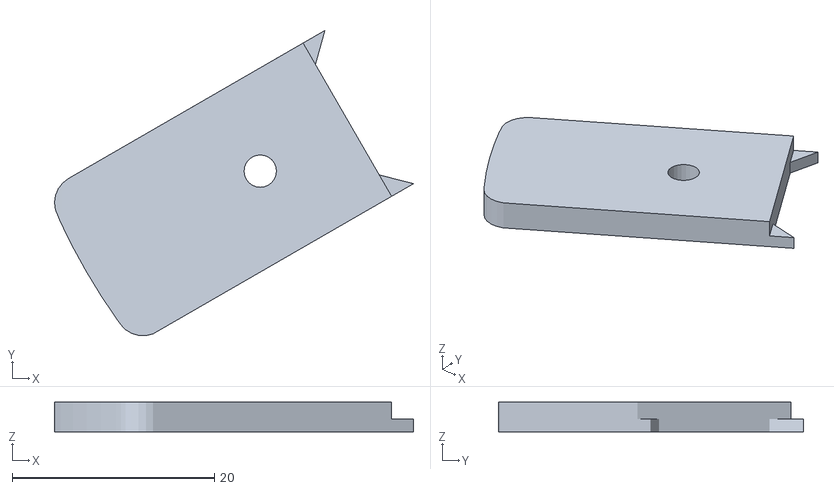
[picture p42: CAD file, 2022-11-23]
unit_purifier/unit_inner/unit_nano/print_holder_nano_2.stl
35.5 x 30.2 x 2.93

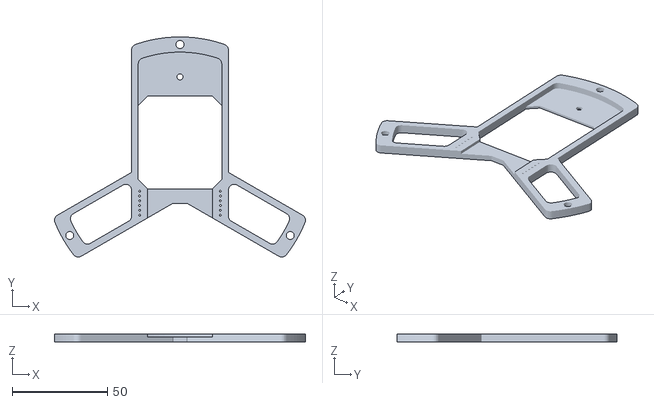
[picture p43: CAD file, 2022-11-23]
unit_purifier/unit_inner/unit_power/print_holder_power_1.stl
132.1 x 115.9 x 4.40

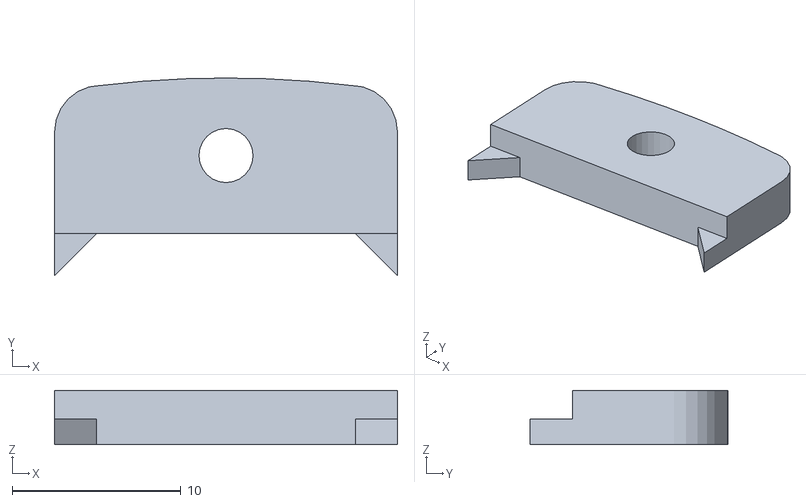
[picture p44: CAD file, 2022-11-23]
unit_purifier/unit_inner/unit_sensors/print_holder_sensors_2.stl
20.3 x 11.7 x 3.21

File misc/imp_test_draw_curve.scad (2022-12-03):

section_radius_outer = 65.0;
section_center_outer = 115.0;
section_angles_outer = [10, 53.8];

section_radius_inner = 90.0;
section_center_inner = 115.0;
section_angles_inner = [10, 53.8];

// precision along the resulting body
section_angles_count = 50;

// precision across the resulting body
stepCount = 15;
stepSize = 1 / stepCount; // 0.50; 

// for given angle, center and radius calculate the x coordinate of a point on the rotational section
function getXSection(angle, center, radius) = center - radius * cos(angle);

// for given angle, center and radius calculate the y coordinate of a point on the rotational section
function getYSection(angle, center, radius) = radius * sin(angle);

// given the input parameters (on the section plane), calculate a 3D coordinate
function getSectionCoordinate(xSection, ySection, angleFraction, sectionFraction, angleMultiplier, angleF, offsetDistance) =
    // rotates by y-coordinate (effectively just spiraling up)
    let (angleA = ySection * 0.5)
    // TODO :: magic numbers => move to variables
    let (angleB = pow(angleFraction + 0.10, 0.5) * angleMultiplier)
    let (angleC = pow(sectionFraction, 2) * 10)
    let (angleD = offsetDistance / (xSection * 2 * PI / 360))
    let (angle2 = angleA + angleB + angleC + angleD + angleF)
    let (xPoly = cos(angle2) * xSection)
    let (yPoly = sin(angle2) * xSection)
    [xPoly, yPoly, ySection];  
 
function getSectionPoints(sectionFraction, angleMultiplier, angleF, offsetDistance) = [
    // the section angle along the outer curve
    let (aSection0 = section_angles_outer[0] - (section_angles_inner[0] - section_angles_outer[0]) * sectionFraction)
    // the section angle along the inner curve
    let (aSection1 = section_angles_inner[1] - (section_angles_inner[1] - section_angles_outer[1]) * sectionFraction)
    // split by section_angles_count along the section curve
    for(i = [0:1:section_angles_count])
        let (angleFraction = i / section_angles_count)
        // section angle as of section curve and current step
        let (aSection = aSection0 - (aSection0 - aSection1) * angleFraction)
        // center as of section curve and current step
        let (cSection = section_center_inner - (section_center_inner - section_center_outer) * sectionFraction)
        // radius as of section curve and current step
        let (rSection = section_radius_inner - (section_radius_inner - section_radius_outer) * sectionFraction)
        // x on the flat section curve
        let (xSection = getXSection(aSection, cSection, rSection))
        // y on the flat section curve
        let (ySection = getYSection(aSection, cSection, rSection))
        getSectionCoordinate(xSection, ySection, angleFraction, sectionFraction, angleMultiplier, angleF, offsetDistance)
    ];
    
// flattens an array by one level of depth
function flatten(l) = [ for (a = l) for (b = a) b ] ;

    
module plotPolyhedron1(angle, angleMultiplier, offsetDistance) {
    points = [
        for(s = [0:stepSize:1])
            getSectionPoints(s, angleMultiplier, angle, offsetDistance)
    ];
    faces_outer = [
        for(s = [0:1:stepCount - 1])
            for(a = [0:1:section_angles_count - 1])
                let (index0 = (section_angles_count + 1) * s)
                let (index1 = (section_angles_count + 1) * (s + 1))
                [a + index0, a + index0 + 1, a + index1 + 1]
    ];
    faces_inner = [
        for(s = [0:1:stepCount - 1])
            for(a = [0:1:section_angles_count - 1])
                let (index0 = (section_angles_count + 1) * s)
                let (index1 = (section_angles_count + 1) * (s + 1))
                [a + index1 + 1, a + index1, a + index0]
    ];        
    faces = concat(faces_outer, faces_inner);  
    polyhedron(points=flatten(points), faces=faces);
}

module plotPolyhedron2(sectionFraction, angle1, angleMultiplier1, offsetDistance1, angle2, angleMultiplier2, offsetDistance2) {
    angleD = angle2 - angle1;
    points = [
        for(s = [0:stepSize:1])
            let (angleMultiplier = angleMultiplier1 + (angleMultiplier2 - angleMultiplier1) * s)
            let (angleFixed = angle1 + (angle2 - angle1) * s)
            let (offsetDistance = offsetDistance1 + (offsetDistance2 - offsetDistance1) * s)
            getSectionPoints(sectionFraction, angleMultiplier, angleFixed, offsetDistance)
    ];
    faces_outer = [
        for(s = [0:1:stepCount - 1])
            for(a = [0:1:section_angles_count - 1])
                let (index0 = (section_angles_count + 1) * s)
                let (index1 = (section_angles_count + 1) * (s + 1))
                [a + index0, a + index0 + 1, a + index1 + 1]
    ];
    faces_inner = [
        for(s = [0:1:stepCount - 1])
            for(a = [0:1:section_angles_count - 1])
                let (index0 = (section_angles_count + 1) * s)
                let (index1 = (section_angles_count + 1) * (s + 1))
                [a + index1 + 1, a + index1, a + index0]
    ];        
    faces = concat(faces_outer, faces_inner);  
    polyhedron(points=flatten(points), faces=faces);
}



// for(p = [0:36:360])
plotPolyhedron1(0, 90, 0.8);
plotPolyhedron1(36, 90, -0.8);

plotPolyhedron2(0, 0, 90, 0.8, 36, 90, -0.8);
plotPolyhedron2(1, 0, 90, 0.8, 36, 90, -0.8);

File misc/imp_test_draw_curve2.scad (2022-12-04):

// precision along the resulting body
section_angles_count = 50;

sectionDefOO = [63.4, 115.0, 10.0, 54.0]; // outer faces of the outer impeller shell
sectionDefOI = [65.0, 115.0, 10.0, 54.0]; // inner faces of the outer impeller shell

sectionDefII = [90.0, 115.0, 10.0, 54.0]; // inner faces of the inner impeller shell
sectionDefIO = [91.6, 115.0, 10.0, 54.0]; // outer faces of the inner impeller shell

sectionDefOS = [sectionDefOO, sectionDefOI]; // outer shell
sectionDefWN = [sectionDefOI, sectionDefII]; // wings
sectionDefIS = [sectionDefII, sectionDefIO]; // inner shell

indexOuter = 0;
indexInner = 1;

// for given angle, center and radius calculate the x coordinate of a point on the rotational section
function getXSection(angle, center, radius) = center - radius * cos(angle);

// for given angle, center and radius calculate the y coordinate of a point on the rotational section
function getYSection(angle, center, radius) = radius * sin(angle);

function getFSection(radius) = (radius - 65.0) / (90.0 - 65.0);

// given the input parameters (on the section plane), calculate a 3D coordinate
function getSectionCoordinate(xSection, ySection, angleFraction, sectionFraction, angleF, offsetDistance) =
    // rotates by y-coordinate (effectively just spiraling up)
    let (angleA = ySection * 0.5) // ySection * 0.5
    let (angleB = pow(angleFraction + 0.10, 0.5) * 90) // pow(angleFraction + 0.10, 0.5) * 90
    let (angleC = pow(1 - sectionFraction, 2) * 10  ) // pow(1 - sectionFraction, 2) * 10 
    let (angleD = offsetDistance / (xSection * 2 * PI / 360)) // offsetDistance / (xSection * 2 * PI / 360)
    let (angle2 = angleA + angleB + angleC + angleD + angleF)
    let (xPoly = cos(angle2) * xSection)
    let (yPoly = sin(angle2) * xSection)
    [xPoly, yPoly, ySection];  
 
function getSectionPoints(radius, angleF, offsetDistance, sectionDef) = [
    // the section angle along the outer curve
    let (sectionFraction = getFSection(radius))
    let (aSection0 = sectionDef[indexInner][2] - (sectionDef[indexOuter][2] - sectionDef[indexInner][2]) * sectionFraction)
    // the section angle along the inner curve
    let (aSection1 = sectionDef[indexOuter][3] - (sectionDef[indexOuter][3] - sectionDef[indexInner][3]) * sectionFraction)
    // split by section_angles_count along the section curve
    for(i = [0:1:section_angles_count])
        let (angleFraction = i / section_angles_count)
        // section angle as of section curve and current step
        let (aSection = aSection0 - (aSection0 - aSection1) * angleFraction)
        // center as of section curve and current step
        let (cSection = sectionDef[indexOuter][1] - (sectionDef[indexOuter][1] - sectionDef[indexInner][1]) * sectionFraction)
        // radius as of section curve and current step
        // let (rSection = sectionDef[indexOuter][0] - (sectionDef[indexOuter][0] - sectionDef[indexInner][0]) * sectionFraction)
    let (rSection = radius)
        // x on the flat section curve
        let (xSection = getXSection(aSection, cSection, rSection))
        // y on the flat section curve
        let (ySection = getYSection(aSection, cSection, rSection))
        getSectionCoordinate(xSection, ySection, angleFraction, sectionFraction, angleF, offsetDistance)
    ];
    
// flattens an array by one level of depth
function flatten(l) = [ for (a = l) for (b = a) b ] ;

    
module plotPolyhedron1(angle, offsetDistance, stepCount, sectionDef) {
    
    stepSize = 1 / stepCount;
    // echo(stepSize);
    points = [
        for(s = [0:stepSize:1])
            let (radius = sectionDef[0][0] + (sectionDef[1][0] - sectionDef[0][0]) * s)
            // echo(radius)
            // echo(getFSection(radius))
            getSectionPoints(radius, angle, offsetDistance, sectionDef)
    ];
        
    faces_outer = [
        for(s = [0:1:stepCount - 1])
            let (index0 = (section_angles_count + 1) * s)
            let (index1 = (section_angles_count + 1) * (s + 1))
            for(a = [0:1:section_angles_count - 1])
                [a + index0, a + index1 + 0, a + index1 + 1]
    ]; 
    faces_inner = [
        for(s = [0:1:stepCount - 1])
            let (index0 = (section_angles_count + 1) * s)
            let (index1 = (section_angles_count + 1) * (s + 1))
            for(a = [0:1:section_angles_count - 1])
                [a + index0, a + index1 + 1, a + index0 + 1]
    ];        
    faces = concat(faces_outer, faces_inner);  
    polyhedron(points=flatten(points), faces=faces);
}

module plotPolyhedron2(radius, angle1, offsetDistance1, angle2, offsetDistance2, stepCount, sectionDef) {
    stepSize = 1 / stepCount;
    angleD = angle2 - angle1;
    points = [
        for(s = [0:stepSize:1])
            let (angleFixed = angle1 + (angle2 - angle1) * s)
            let (offsetDistance = offsetDistance1 + (offsetDistance2 - offsetDistance1) * s)
            // echo(radius)
            // echo(getFSection(radius))        
            getSectionPoints(radius, angleFixed, offsetDistance, sectionDef)
    ];
    faces_outer = [
        for(s = [0:1:stepCount - 1])
            let (index0 = (section_angles_count + 1) * s)
            let (index1 = (section_angles_count + 1) * (s + 1))
            for(a = [0:1:section_angles_count - 1])
                [a + index0 + 1, a + index1 + 1, a + index1 + 0]
    ];
    faces_inner = [
        for(s = [0:1:stepCount - 1])
            let (index0 = (section_angles_count + 1) * s)
            let (index1 = (section_angles_count + 1) * (s + 1))
            for(a = [0:1:section_angles_count - 1])
                [a + index0  + 1, a + index1 + 0, a + index0 + 0]
    ];     
    faces = concat(faces_outer, faces_inner);  
    polyhedron(points=flatten(points), faces=faces);
}



// wing portruding out
// plotPolyhedron1(0, 1, 1, sectionDefOS);
// plotPolyhedron1(0, -1, 1, sectionDefOS);
plotPolyhedron2(sectionDefOS[indexOuter][0], 0, -1, 0, 1, 1, sectionDefOS);
// plotPolyhedron2(sectionDefWN[indexOuter][0], 0, -1, 0, 1, 1, sectionDefWN);
// plotPolyhedron2(sectionDefOS[indexOuter][0], 0, 1, 36, -1, 16, sectionDefOS);
// plotPolyhedron2(sectionDefWN[indexOuter][0], 0, 1, 36, -1, 16, sectionDefWN);

// main wing
// plotPolyhedron1(0, 1, 16, sectionDefWN);
// plotPolyhedron1(0, -1, 16, sectionDefWN);

// wing portruding in
// plotPolyhedron1(0, 1, 1, sectionDefIS);
// plotPolyhedron1(0, -1, 1, sectionDefIS);
// plotPolyhedron2(sectionDefIS[indexInner][0], 0, -1, 0, 1, 1, sectionDefWN);
// plotPolyhedron2(sectionDefWN[indexInner][0], 0, -1, 0, 1, 1, sectionDefIS);
// plotPolyhedron2(sectionDefIS[indexInner][0], 0, 1, 36, -1, 16, sectionDefIS);
// plotPolyhedron2(sectionDefWN[indexInner][0], 0, 1, 36, -1, 16, sectionDefWN);

// main borders
// plotPolyhedron2(sectionDefWN[indexInner][0], 0, 1, 36, -1, 16, sectionDefWN);
// plotPolyhedron2(sectionDefWN[indexOuter][0], 0, 1, 36, -1, 16, sectionDefWN);

// portruded border (outer)
// plotPolyhedron2(sectionDefOS[indexOuter][0], 0, -1, 0, 1, 1, sectionDefOS);
// portruded border (inner)
// plotPolyhedron2(sectionDefIS[indexInner][0], 0, -1, 0, 1, 1, sectionDefWN);

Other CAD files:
misc/imp_test_draw_curve2_wing_sec_a.stl
unit_purifier/unit_head/print_outer_connect.stl
unit_purifier/unit_inner/unit_sensors/print_holder_sensors_1.stl
unit_purifier/unit_inner/unit_sensors/print_holder_sensors_3.stl
unit_purifier/screws/flat_m3_10.skp
unit_purifier/screws/flat_m3_16.skp
unit_purifier/screws/m4_14_din7984.skp
unit_purifier/screws/nut_m10_14.skp
unit_purifier/screws/nut_m4.skp
unit_purifier/screws/nut_m4_20mm.skp
unit_purifier/unit_cover/print_cover_1.skp
unit_purifier/unit_cover/print_cover_2.skp
unit_purifier/unit_foot/print_outer_foot.skp
unit_purifier/unit_head/print_outer_connect.skp
unit_purifier/unit_head/print_outer_controls.skp
unit_purifier/unit_head/print_outer_outlet.skp
unit_purifier/unit_head/print_outer_ring.skp
unit_purifier/unit_honeycomb/print_honeycomb_1.skp
unit_purifier/unit_honeycomb/print_honeycomb_2.skp
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

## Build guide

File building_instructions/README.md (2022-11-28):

# PRINTABLE PURIFIER BUILDING INSTRUCTIONS

### 1. Hub 1 and Impeller 1
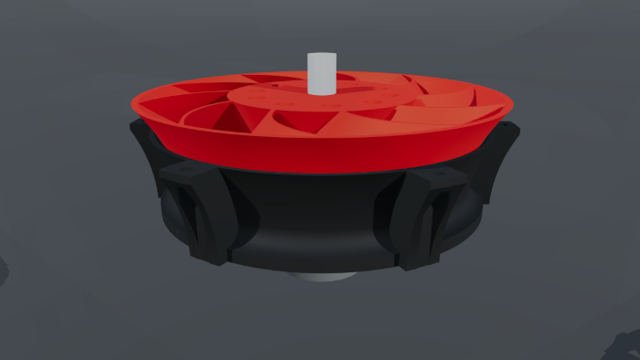
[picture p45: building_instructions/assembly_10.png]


The perhaps most challenging step in this build comes first. Be sure the z-axis of your printer is perpendicular to the bed, or your impeller will get a bad wobble.

Print [Lower hub](../unit_purifier/unit_inner/unit_hub/print_hub_1.stl) and [Lower impeller](../unit_purifier/unit_impeller/print_impeller_1.stl). Note that Lower hub is printed upside down. Use pliers to remove supports from the hub. Make the [Impeller mount](../unit_purifier/unit_inner/unit_motor/lathe_motor_connect.stl) or have it made. A 555-1 type motor is needed and two flat M3 screws to fix the motor to the hub.

The impeller will require balancing after printing. This can be done by adding counterweights to one or more holes provided in the printed impeller. I cut pieces off a 6mm brass rod and used those as counterweights.

I built a very simple balancing tool to find the heavier side of the impeller, but you could also just mount the impeller on a 10mm rod, then put both ends of the rod on horizontal surfaces of equal height. The impeller can then roll back and forth to find its balance. At first the impeller will want to settle in a specific position. Add counterweights until the impeller appears not to have a specific settling point any more.

You can also balance by trial and error while in the hub, but this can be lengthy process requiring a lot of patience.

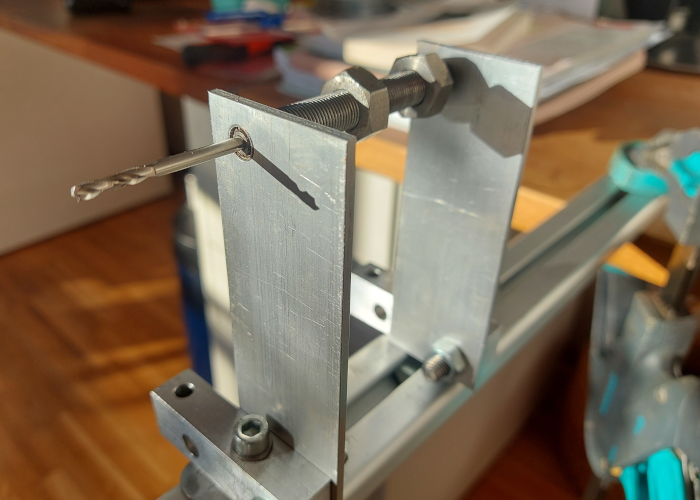
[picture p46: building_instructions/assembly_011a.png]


Insert counterweights into the provided 6mm holes as required until vibration is tolerable when the impeller is powered by the motor and spinning in the hub.

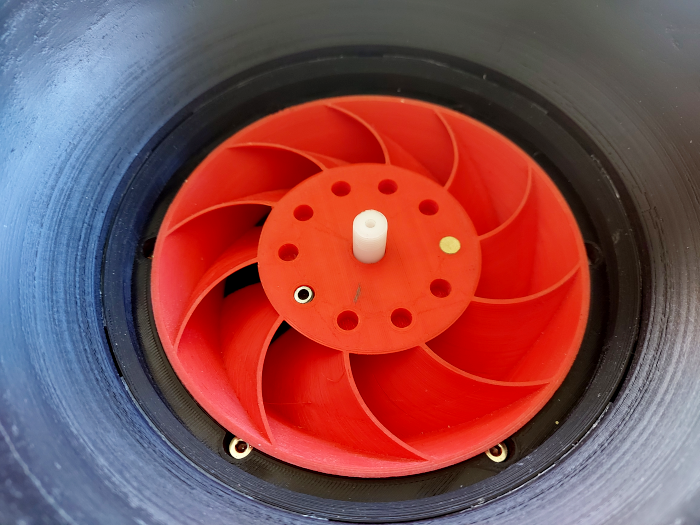
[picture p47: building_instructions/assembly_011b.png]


---

### 2. Hub 2 and Impeller 2

Print [Upper hub](../unit_purifier/unit_inner/unit_hub/print_hub_2.stl) and [Upper impeller](../unit_purifier/unit_impeller/print_impeller_2.stl). M4 screws and 20MM M4 nuts are needed to connect the two hub parts. When you have a hard time finding the long M4 nuts search in electronics supply, these are used in computer builds, so you will hav good chanced to find them there. You will have to use a long M4 screw to pull the nuts into their seat in the lower hub, where they should find a firm fit.

Repeat balancing with the upper impeller.

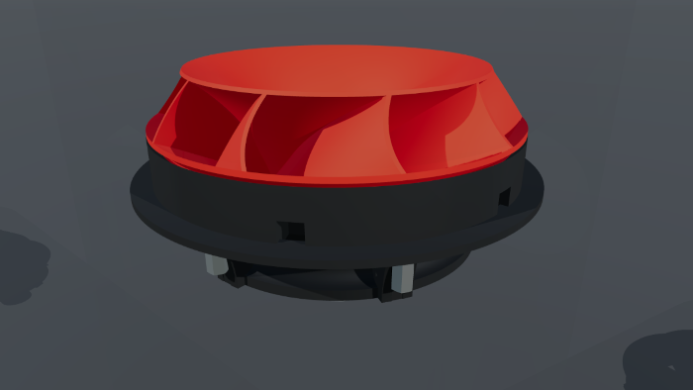
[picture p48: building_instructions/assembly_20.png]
Step 2


---

### 3. Inners

In the next steps the inner parts of the purifier are built.

3.1 Power

Build power unit from the parts listed in [Power](../unit_purifier/unit_inner/unit_power). Connect a ~50cm long power cable (12V) to the VS pin of the L298N controller. Connect ground to the GND pin of the L298N controller. Connect the L298N controllers 5V pin to all six 5V pins (these will later provide power to arduino, sensors, ...). Connect the GND pin of the L298N controller (now there should two cables in the GND pin) to all six GND pins (these will later be the GND pins for arduino, sensors, ...). Connect the power cable to the 5.5x2.1 plug.

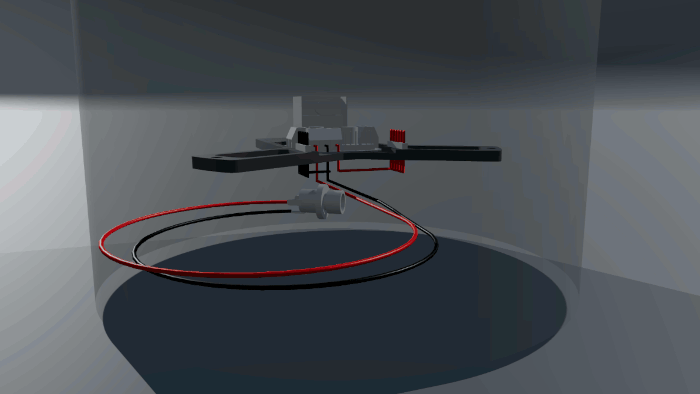
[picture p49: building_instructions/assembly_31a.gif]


Soldering is required to connect the 5V output of the L298N to the power pins, to connect the GND pin to the GND pins and to connect the power cable to the plug.

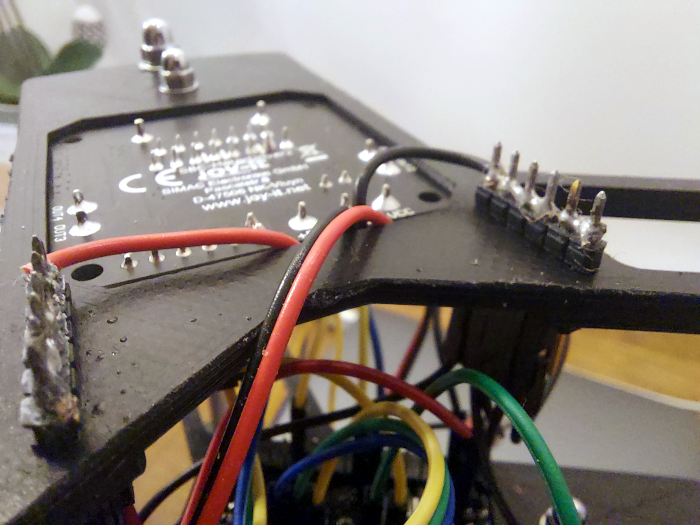
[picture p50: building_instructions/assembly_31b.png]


Please refer to [Interface L298N DC Motor Driver Module with Arduino](https://lastminuteengineers.com/l298n-dc-stepper-driver-arduino-tutorial/) for more information.

3.2 Arduino

Build arduino unit from the parts listed in [Arduino](../unit_purifier/unit_inner/unit_nano). No cables yet.

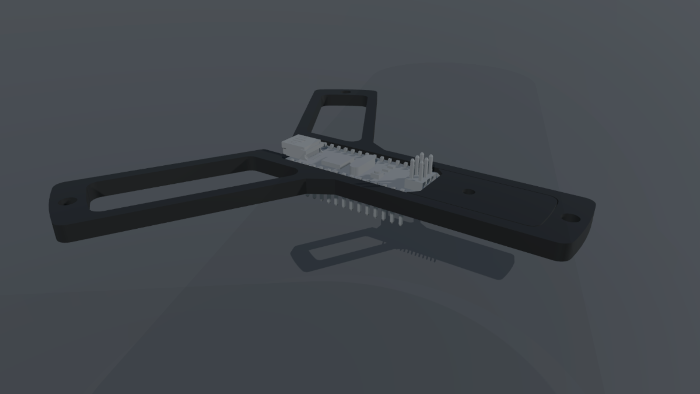
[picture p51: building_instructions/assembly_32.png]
Step 3.2


3.3 Sensors

Build sensor unit from the parts listed in [Sensors](../unit_purifier/unit_inner/unit_sensors).

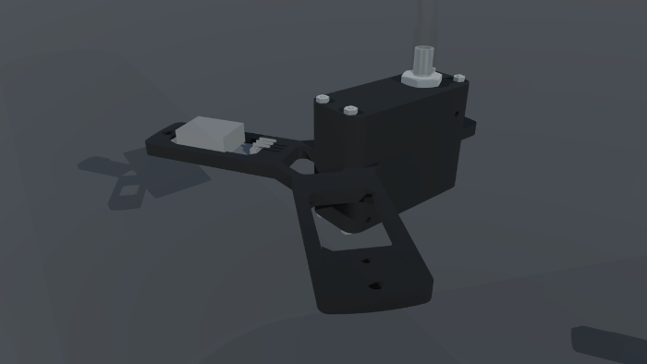
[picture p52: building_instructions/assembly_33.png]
Step 3.3


3.4 Motor

Build Motor assembly from from the parts listed in [Motor assembly](../unit_purifier/unit_inner/unit_motor).

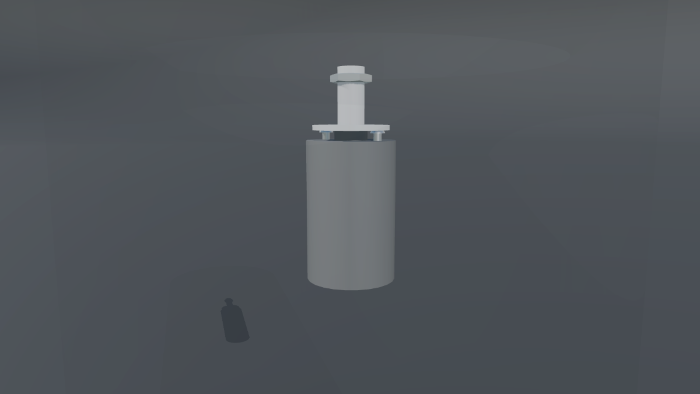
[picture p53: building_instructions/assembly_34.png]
Step 3.4


3.5 Inner Assembly

Assemble hub, motor, sensors, arduino and power units to the full inner unit with the parts listed in [Screws](../unit_purifier/unit_inner/unit_screws).

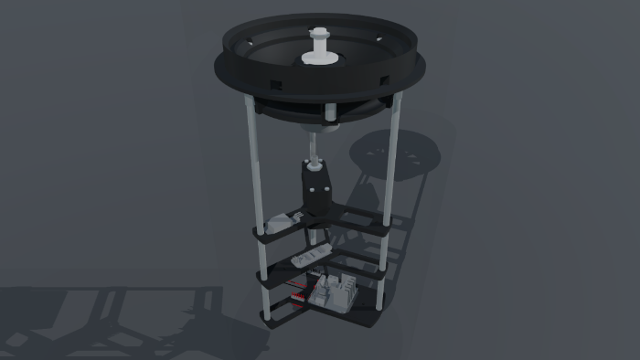
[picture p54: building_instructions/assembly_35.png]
Step 3.5


3.6 Arduino Wiring

Connect the Arduino VIN pin to one of the 5V pins on the power unit. Connect the Arduino GND pin to one of the ground pins on the power unit.

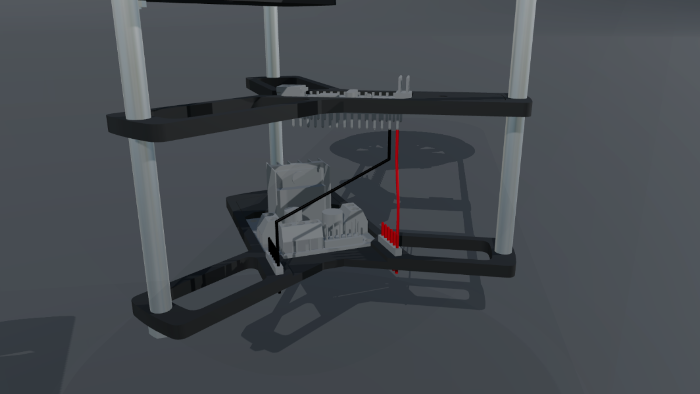
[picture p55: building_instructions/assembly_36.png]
Step 3.6


3.7 Motor wiring

Connect the Arduino D9 pin to the L298N ENA pin. Connect the Arduino D8 pin to the L298N IN1 pin. Connect the Arduino D7 pin to the L298N IN2 pin. Then connect the L298N OUT1 pin to one of the motor's pins and connect the L298N OUT2 pin to the other motor pin. It does not matter which motor pins are connected, you can set motor direction later from the arduino sketch. Please refer to [Interface L298N DC Motor Driver Module with Arduino](https://lastminuteengineers.com/l298n-dc-stepper-driver-arduino-tutorial/) for more information.

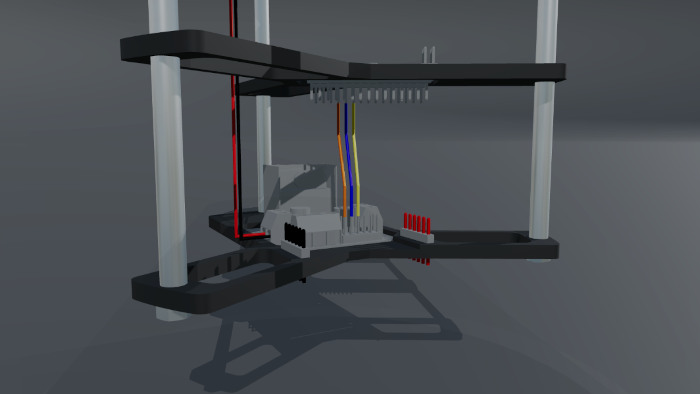
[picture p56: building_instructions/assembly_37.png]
Step 3.7


3.8 Dust Sensor wiring

Connect the Arduino D3 pin to the dust sensor digital cable. Connect the dust sensor power cable to one of the 5V pins. Connect the dust sensor ground cable to one of the ground pins. Please refer to [PM-D4](http://www.csfan.co.kr/bbs/board.php?bo_table=products1&wr_id=15&ckattempt=1) for more information.

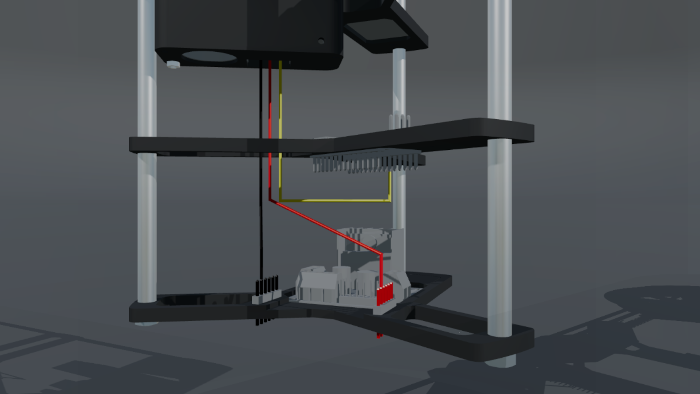
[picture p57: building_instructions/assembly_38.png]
Step 3.8


3.9 Temperature and Humidity Sensor wiring

Connect the Arduino D4 pin to the DHT22 sensor output pin. Connect the DHT22 sensor power pin to one of the 5V pins. Connect the DHT22 sensor GND pin to one of the ground pins. Please refer to [DHT 22](https://joy-it.net/de/products/SEN-DHT22) for more information.

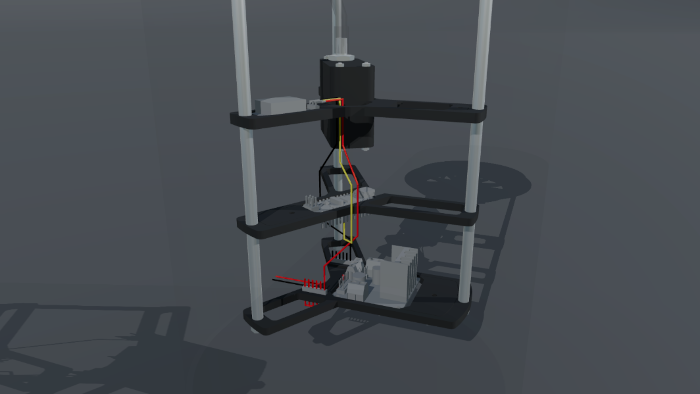
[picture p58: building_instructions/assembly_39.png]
Step 3.9


3.10 Potentiometer wiring

Connect the Arduino A0 pin to a 20cm yellow cable. Connect a 20 cm red cable one of the 5V pins. Connect a 20 cm black cable to one of the ground pins.

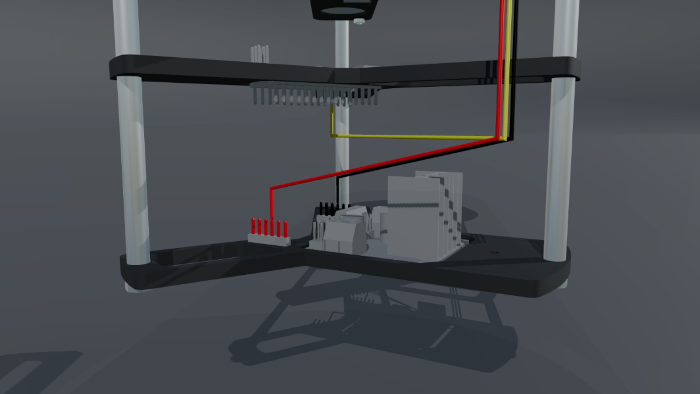
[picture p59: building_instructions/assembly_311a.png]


Solder a 10cm yellow cable to the potentiometer signal pin. Solder a 10cm red cable to the potentiometer VC pin. Solder a 10cm black cable to the potentiometer GND pin. Later the cables from the potentiometer will be stuck through one of the hub openings and connected to the respective inner cables.

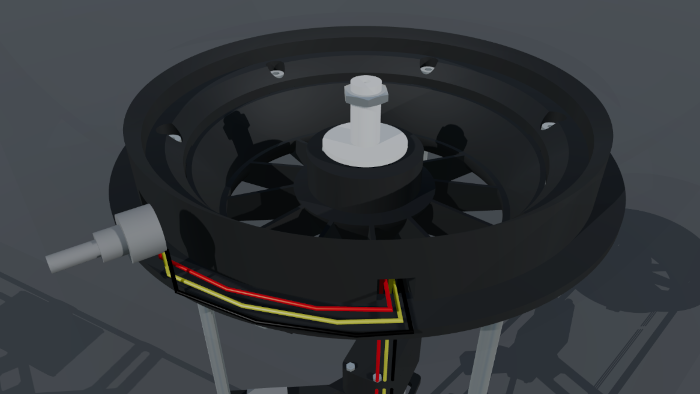
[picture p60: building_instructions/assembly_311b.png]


3.11 Display wiring

Connect the Arduino A4 (SDA) pin to a 20cm yellow cable. Connect the Arduino A5 (SCL) pin to a 20cm blue cable. Connect a 20 cm red cable one of the 5V pins. Connect a 20 cm black cable to one of the ground pins.

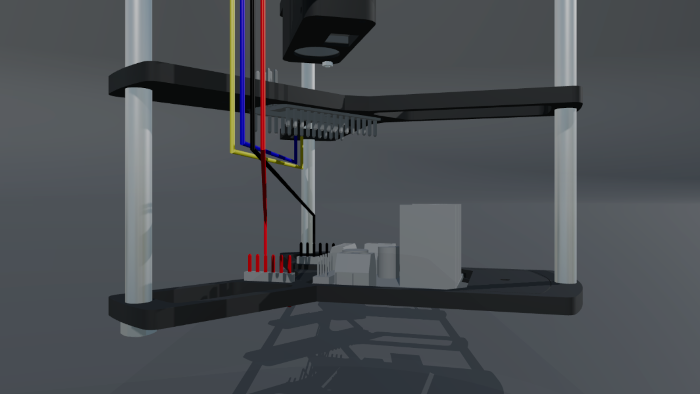
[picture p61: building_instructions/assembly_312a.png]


Connect a 10cm yellow cable to the display's SDA pin.  Connect a 10cm blue cable to the display's SCL pin. Connect a 10cm red cable to the display's VCC pin. Connect a 10cm black cable to the display's GND pin. Later the cables from the display will be stuck through one of the hub openings and connected to the respective inner cables.

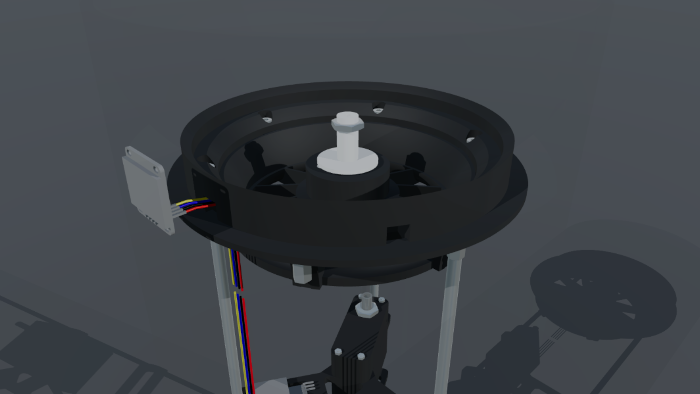
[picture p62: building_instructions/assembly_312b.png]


Please refer to [0.96 INCH OLED SCREEN WITH I2C](https://whadda.com/product/0-96-inch-oled-screen-with-i2c-wpi438/) for more information.

---

### 4. Arduino Sketch

**IMPORTANT: when you are connecting a USB cable to your Arduino, you must disconnect the arduino from the inner power supply, since it will then get it's power through USB. I pulled the VIN cable when uploading new code, but left the GND connected to the motor controller. After the code does what it should disconnect both USB and 12V power supply, then reconnect the VIN cable to the controller, then power up the now standalone system with 12V.**

Please find the arduino sketch that i am using here [Sketch](../code/sketch_purifier/sketch_purifier.ino). I will describe the sketch in more detail when time allows.

---

### 5. Head

In the next steps the head of the purifier is built. Full part list here: [Head](../unit_purifier/unit_head).

5.1 Lower head

Print [Lower head](../unit_purifier/unit_head/print_outer_controls.stl). Note that this part is printed upside down. Use pliers to remove supports, then clean up the the openings for the display and the potentiometer until they fit properly. Remove display and potentiometer again, they will be finally inserted in a later step.

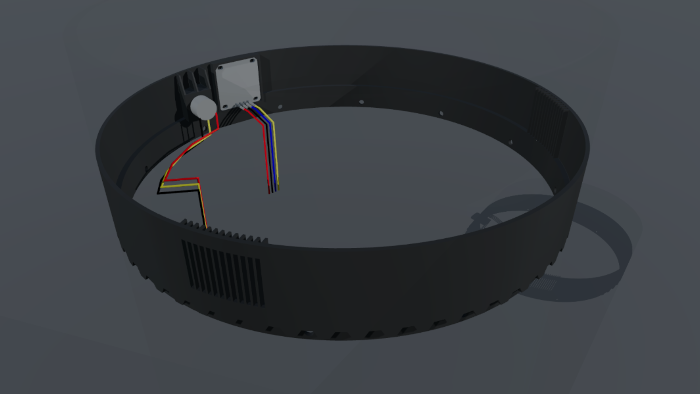
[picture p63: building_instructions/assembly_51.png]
Step 5.1


5.2 Upper head

Print [Upper head](../unit_purifier/unit_head/print_outer_ring.stl). Note that this part is printed upside down. Place The upper head into Lower head and glue them together. Before applying glue, please check that the glue you are using works good with PLA. I used "UHU Hartplastik", which you can get in most hardware stores where i live.

After the glue has dried, sand the outfacing surface of the head, then spray paint the outside in multiple, thin layers. Like with the glue be sure that the spray you are using does not negatively affect your materials.

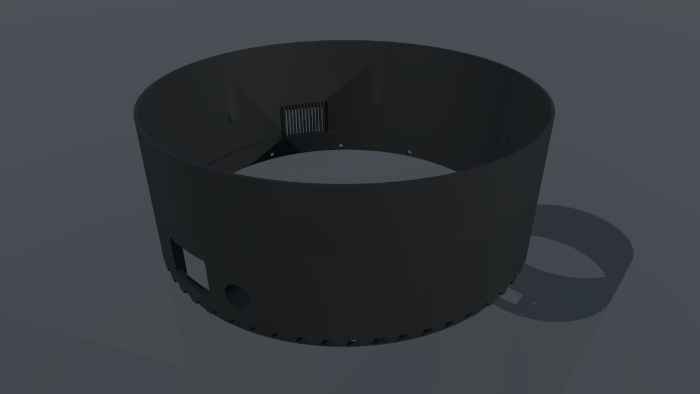
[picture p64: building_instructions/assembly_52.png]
Step 5.2


5.3 Head Connector

Print [Head Connector](../unit_purifier/unit_head/print_outer_connect.stl). Note that the part is printed upside down. Cut a piece of 2mm foam rubber to match the bottom surface, cut holes where screws and cable outlets are, then glue the foam rubber in place. Again be sure the glue does not harm both foam rubber and PLA.

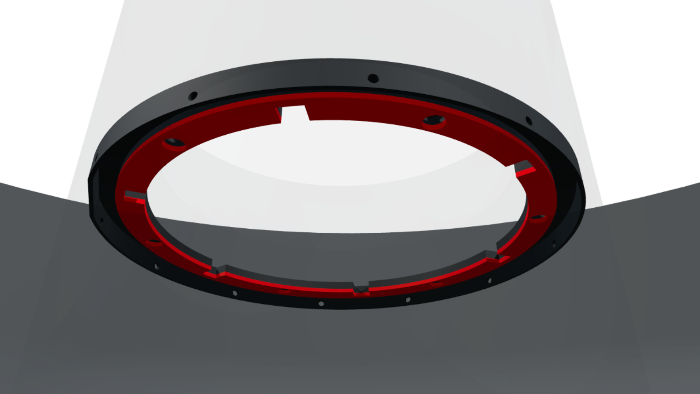
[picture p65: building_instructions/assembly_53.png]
Step 5.3


5.4 Inner Head

Print [Inner Head](../unit_purifier/unit_head/print_outer_outlet.stl). Note that the part is printed upside down. Use a 4mm drill to open the screwholes in this part. Use a M4 screw of appropriate length to pull M4 nuts into their seats in this part. Sand inner surface and spray paint for a good surface finish.

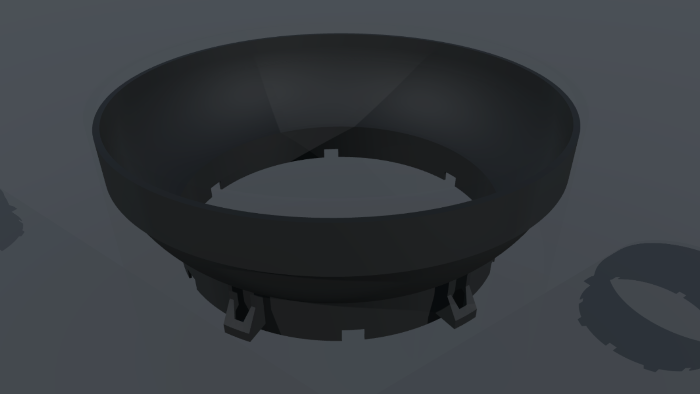
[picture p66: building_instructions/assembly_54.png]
Step 5.4


5.5 Head Assembly

Reinsert display and potentiometer into the outer ring. Use the nut provided with the potentiometer to tighten it in place. Slide in the flat connector ring from underneath. Slide in the Inner head from the upside. Be careful not to harm the display and potentiometer cables, which should be passing through adjacent cable outlets now.

Use M4 screws to screw the connector and the inner part together. When done, the purifier head should look like this.

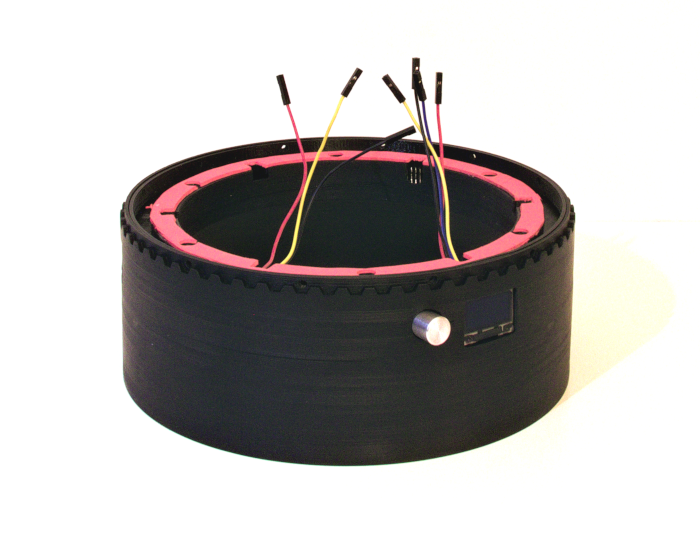
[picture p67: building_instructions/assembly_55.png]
Step 5.5


---

### 6. Head

Let's add a housing around the filter. I split the housing into 6 parts to split up printer time a bit. If you have a printer that can handle large parts with enough precision, you could just merge some parts to save sanding at the part junctions. Full part list here: [Housing](../unit_purifier/unit_honeycomb).

6.1 Lower housing

Print [Lower housing](../unit_purifier/unit_honeycomb/print_honeycomb_1.stl). Use pliers to remove supports, then clean the upper and lower bounds with file and sandpaper. I used sandpaper wrapped around a 5mm allen key, thus being able to sand multiple surfaces at once. Cleaning up the hexagon boundary is quite a lot of work, but it ensures a good fit between the housing parts, when they are glued together in a later step.

Widen the 1mm holes to 2mm, then to 3mm. Be careful doing so, but don't worry if one of the hexagons breaks while drilling.

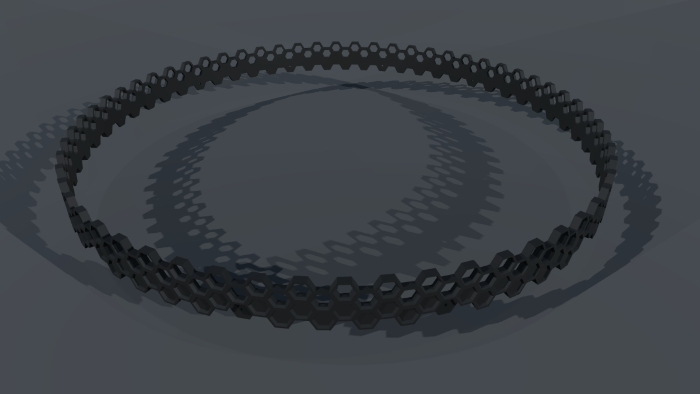
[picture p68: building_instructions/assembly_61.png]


6.2 Center housing

Print 4 pieces of [Center housing](../unit_purifier/unit_honeycomb/print_honeycomb_2.stl). Remove supports and apply the cleanup steps described in 6.1.

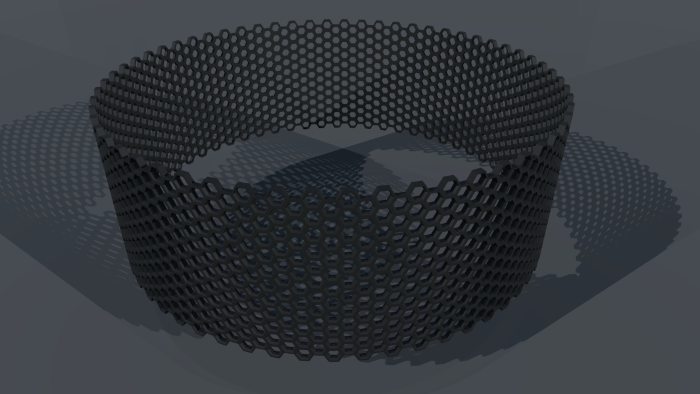
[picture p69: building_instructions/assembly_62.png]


6.3 Upper housing

Print [Upper housing](../unit_purifier/unit_honeycomb/print_honeycomb_3.stl). Remove supports and apply the cleanup steps described in 5.1., open the 1mm holes to 3mm as described in 5.1.

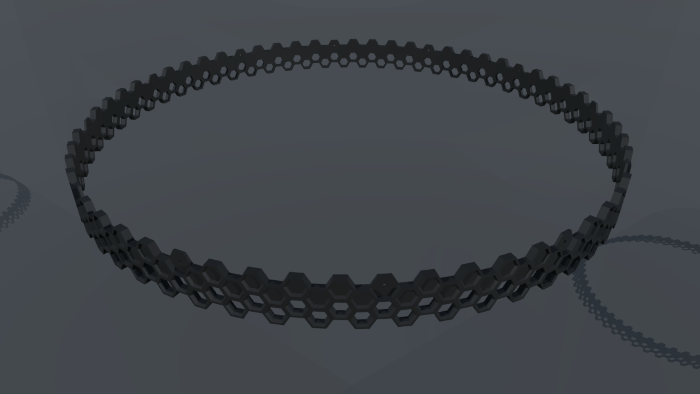
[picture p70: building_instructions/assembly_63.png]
Step 6.3


6.4 Housing Assembly

After careful sanding all 6 parts will have a good fit and can be glued together. Be sure to use glue that does not affect PLA negatively, ie. "UHU Hartplastik". Go in steps, apply glue to the lower part, attach the upper part, ensure good alignment then apply pressure i.e. by placing a large book on the upper part, settle, iterate.

Sand the outside of the assembled housing, spray paint for a good finish.

Expect the housing to look like so.

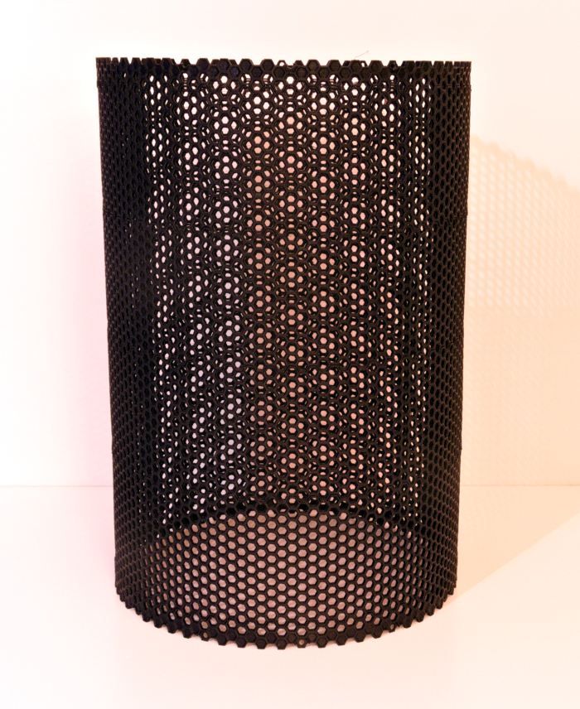
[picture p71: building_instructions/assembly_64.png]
Step 6.4


---

### 7. Foot

Print [Foot](../unit_purifier/unit_foot/print_outer_foot.stl). Use pliers to clear the hole for the power plug, then cut an 8x1 thread to accomodate the plug's thread. Sand and spray paint for a good finish. Cut 2mm foam rubber to fit both upper and lower side of the foot, then glue it onto the respective surfaces. Again, be sure to use glue that does not interfere with PLA or foam rubber.

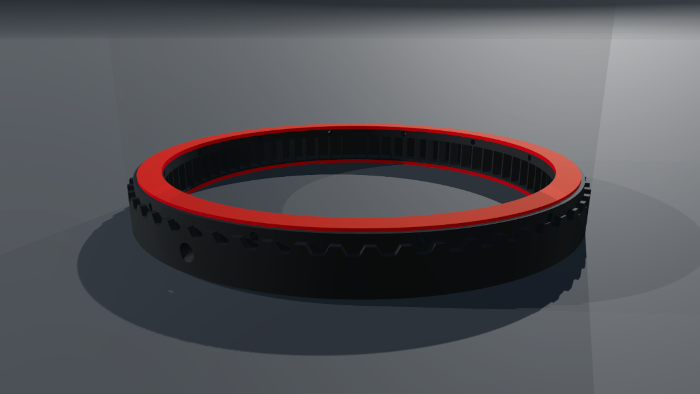
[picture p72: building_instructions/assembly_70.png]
Step 7


---

### 8. Filter

Cut 2mm foam rubber to fit the filter's ~160m diameter top area and glue it to the filter. Depending on the final height of your housing build you may need 2 layers of foam rubber here. Drill a 12mm hole into the bottom of your filter to allow the power cable to exit.

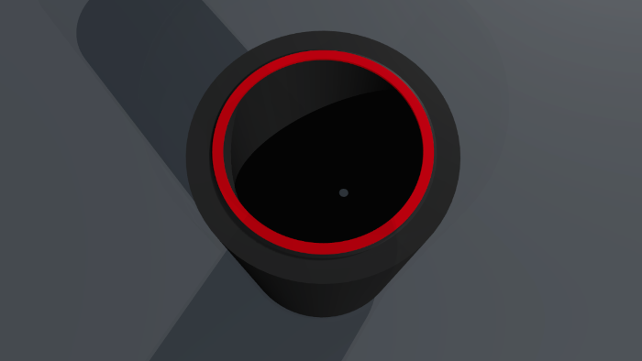
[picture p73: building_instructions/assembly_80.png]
Step 8


---

### 9. Cover

Print [Impeller cover](../unit_purifier/unit_cover/print_cover_1.stl) and [Customizeable cover](../unit_purifier/unit_cover/print_cover_2.stl). Sand and spray paint the center for a good finish.

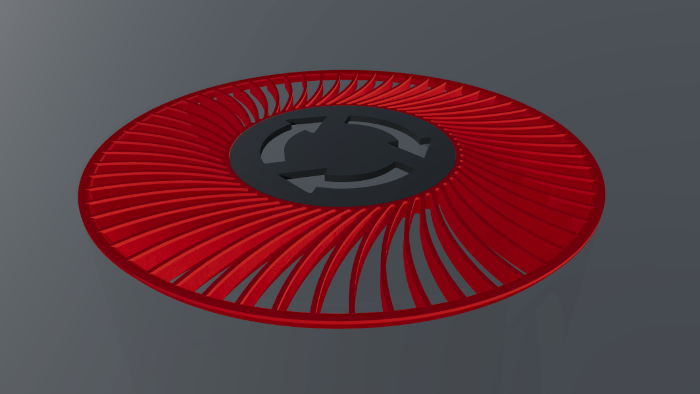
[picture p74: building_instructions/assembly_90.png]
Step 9


---

### 10. Final assembly

Now everything is ready to assemble your purifier to a fully functional device.

10.1 Attach Head to Inner

Slide the head assembly onto the inner assembly. While doing so, put the display and potentiometer cables through their respective outlets. Once the head assembly is seated, connect the 10cm display and potentiometer cable with their 20cm internal counterparts.

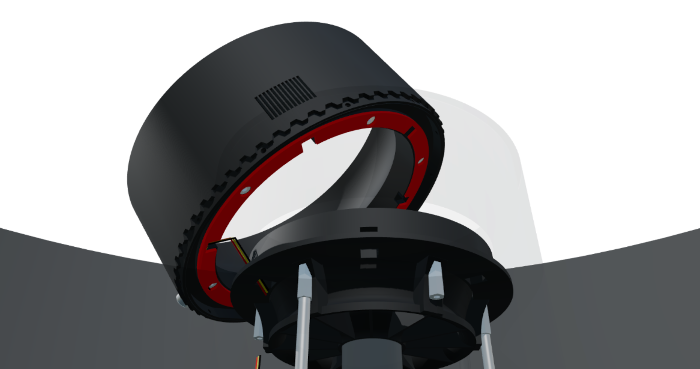
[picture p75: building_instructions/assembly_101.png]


10.2 Insert distance holders

I had the issue that Head and Hub would not be concentric, so i inserted stripes that i had cut from a plastic bottle. The occasional impeller rub went away after inserting the stripes.

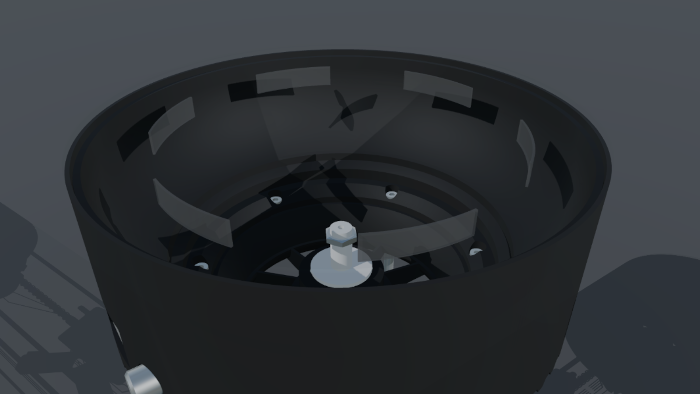
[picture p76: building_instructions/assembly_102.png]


10.3 Upside down

Press Head assembly and Inner assembly against each other and turn everthing upside down. The Inner assembly should now rest on the Head assembly.

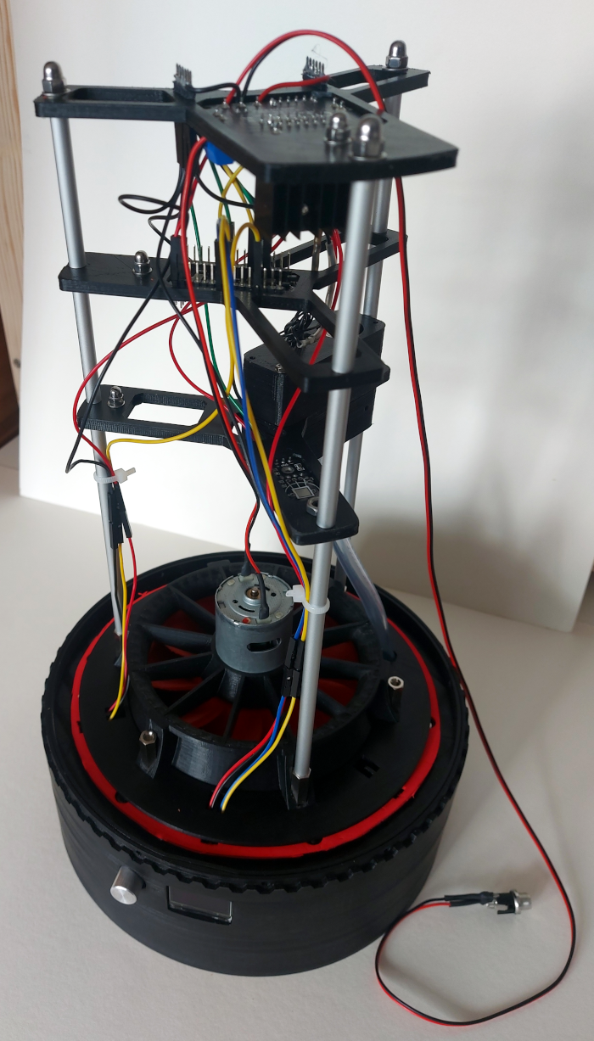
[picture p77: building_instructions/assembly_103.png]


10.4 Add filter

Slide the power cable through the 12mm hole in the filter bottom (see Step 8) and lower the filter onto the Inner assembly.

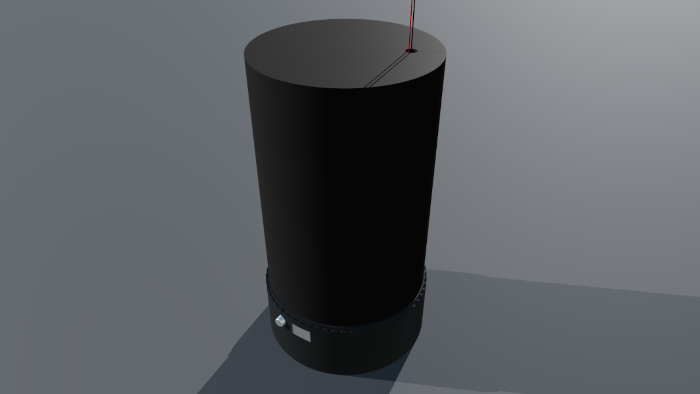
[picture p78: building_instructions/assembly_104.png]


10.5 Add Housing

Lower the housing onto the assembly, be sure that the holes in the housing align with the holes in the Head assembly. Insert M3 lenshead screws to attach housing.

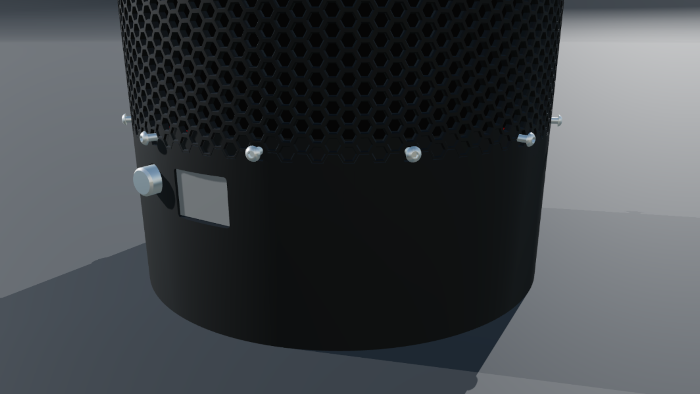
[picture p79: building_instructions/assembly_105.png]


10.6 Add Foot

Attach the Foot assembly using M3 lenshead screws. Screw the power cable plug into the M8x1 foot from the inside. Push the remaining power cable back into the filter, then close the 12mm hole with tape.

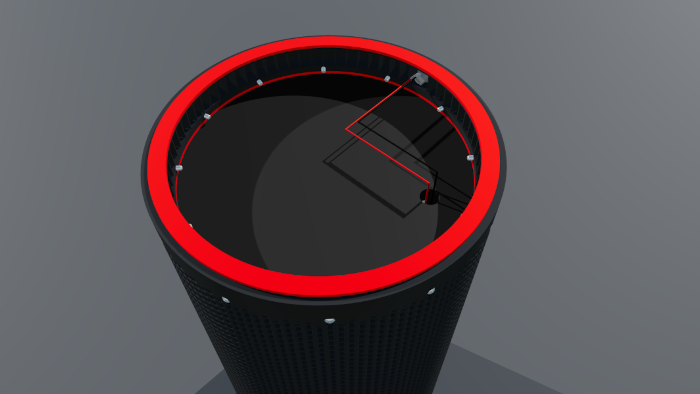
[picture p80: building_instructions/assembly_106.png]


10.7 Turn back around, add Impeller and Cover

Turn the purifier back to it's upright position, insert the Impeller assembly and tighten with M10 nut. Insert the Cover assembly to complete assembly.

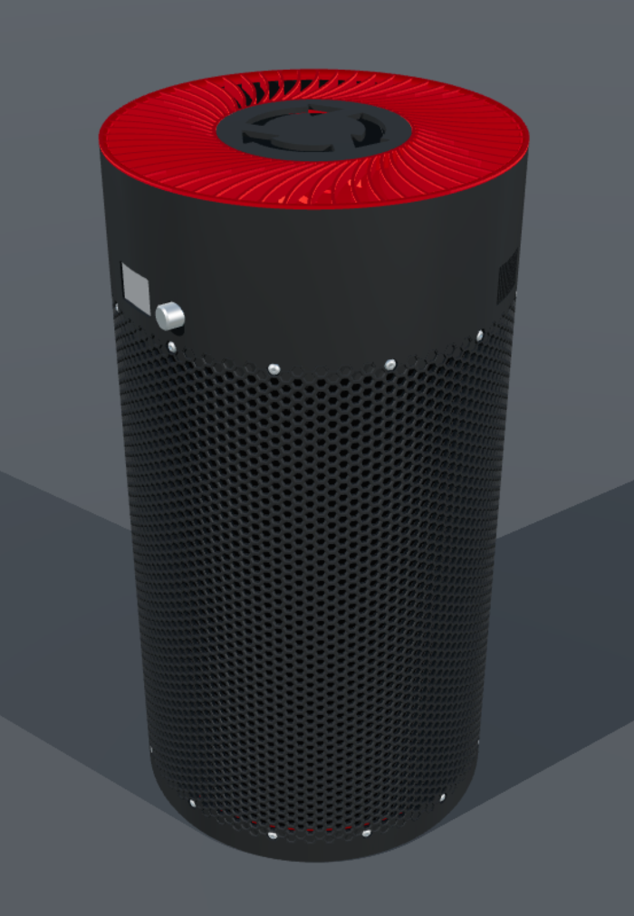
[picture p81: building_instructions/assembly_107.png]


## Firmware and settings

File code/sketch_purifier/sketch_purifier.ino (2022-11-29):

#include "U8glib.h" // display
#include "DHT.h" // temperature and humidity
#include <SoftwareSerial.h>

// port of dht sensor (digital)
#define PORT_____SENSOR_DHT 4

// port of potentiometer (analog)
#define PORT__POTENTIOMETER A0

// ports of dust sensor (digital)
#define PORT_SENSOR_DUST_RX 3
#define PORT_SENSOR_DUST_TX 2

// ports of motor controller (digital, 9 is pwm)
// ports 9 and 10 appear to be connected by the underlying timer, so 10 should probably be left alone
#define PORT____MOTOR_SPEED 9
#define PORT____MOTOR_DIR_1 8
#define PORT____MOTOR_DIR_2 7

// initialize display (see documentation at https://www.velleman.eu/products/view/?id=460516)
U8GLIB_SSD1306_128X64 u8g(U8G_I2C_OPT_NO_ACK);

// initialize dust sensor
SoftwareSerial SENSOR_DUST = SoftwareSerial(PORT_SENSOR_DUST_RX, PORT_SENSOR_DUST_TX);
char BUFFER_SENSOR_DUST[128];

// initialize dht sensor
DHT SENSOR_DHT(PORT_____SENSOR_DHT, DHT22); // DHT22 is a global coming with DHT.h include

// vertical position of PM2.5 value on display
const int DISPLAY_TEXT_A = 19;
// vertical position of °C and %RH value on display
const int DISPLAY_TEXT_B = 63;

const int DISPLAY_LINE_A = 33;
const int DISPLAY_LINE_B = 39;
const int DISPLAY_LINE_C = 45;

// used for formatting strings with leading zeros
const String STRING_PAD_BLANK_4 = "   ";
const String STRING_PAD_BRACK_4 = "          ";
char CHAR_BUF[32];

// current value of the potentiometer (on a range from 0-1023)
int valuePoti = 0;

// current PM2.5 sensor value
int valueIndexPm25 = 0;
int valuePm25 = 0;
int valueArrayPm25[10];

// current DHT sensor values
int valueHumidity = 0;
float valueTemperature = 0;

// a timestamp where the motor power can be reduced after a startup
long tsMotorStart = -1;
int valueMotorMin = 0;
int valueMotorMax = 511;

// current motor value (on a range from 0-1023), needs to be mapped to valueMotorMin (as of calibration) and valueMotorMax
int valueMotorCur = 0;
int valueMotorDst = 0;

void setup(void) {

  // set baud rate for serial monitor (for development)
  Serial.begin(9600);

  // does nothing
  setupPotentionmeter();

  // have the display ready to show calibration info
  setupDisplay();

  // get the dust sensor up
  setupSensorDust();
  setupSensorDht();

  // setup motor
  setupMotor();

}

/*
 * setup anything potentiometer related (nothing currently)
 */
void setupPotentionmeter() {
  // do nothing
}

/*
 * start the display
 */
void setupDisplay() {
  u8g.setRot180(); // flip screen
  u8g.setColorIndex(1); // u8g.getMode() = U8G_MODE_BW
}

void setupMotor() {

  // Mehr Infos: https://arduino-projekte.webnode.at/registerprogrammierung/fast-pwm/
  // Löschen der Timer/Counter Control Register A und B
  TCCR1A = 0;
  TCCR1B = 0;

  // TODO :: re-check values from documentation
  TCCR1A |= (1 << WGM11);
  TCCR1B |= (1 << WGM12);

  // Vorteiler auf 1 setzen (?)
  TCCR1B |= (1 << CS10);

  // Nichtinvertiertes PWM-Signal setzen
  TCCR1A |= (1 << COM1A1);

   // PWM-Pin 9 als Ausgang definieren
  DDRB |= (1 << DDB1);

  // set pin modes for motor ports
  pinMode(PORT____MOTOR_SPEED, OUTPUT);
  pinMode(PORT____MOTOR_DIR_1, OUTPUT);
  pinMode(PORT____MOTOR_DIR_2, OUTPUT);

  startMotor();

}

void startMotor() {
  tsMotorStart = millis();
  valueMotorMin = 310; // have a short period of higher power to ensure proper startup
  digitalWrite(PORT____MOTOR_DIR_1, LOW);
  digitalWrite(PORT____MOTOR_DIR_2, HIGH);
}

/**
  * start the dust sensor (port modes and actual start by baud rate)
  */
void setupSensorDust() {
  pinMode(PORT_SENSOR_DUST_RX, INPUT);
  pinMode(PORT_SENSOR_DUST_TX, OUTPUT);
  SENSOR_DUST.begin(9600);
}

/**
  * start the dht sensor (by calling api method)
  */
void setupSensorDht() {
  SENSOR_DHT.begin();
}

/**
  * maps the motor value (0-1023) into the valid motor power range (valueMotorMin -> valueMotorMax)
  */
void applyMotorSpeed() {
  OCR1A = map(valueMotorCur, 0, 1023, valueMotorMin, valueMotorMax);
}

void loop(void) {

  readPotentiometer();

  // after a startup period - settle valueMotorMin
  if (millis() > tsMotorStart + 2000) {
    valueMotorMin = 285;
  }

  // read dust sensor value
  readSensorDust();
  // read temperature and humidity
  readSensorDht();

  calculateMotorValue();
  applyMotorSpeed();

  u8g.firstPage();
  do {
    redrawDisplayLoop();
  } while (u8g.nextPage());

  delay(1000);

}

/**
  * read (and invert) the potentiometer value, so 0 is on the very ccw position
  */
void readPotentiometer() {
  valuePoti = 1023 - analogRead(PORT__POTENTIOMETER);
}

/**
  * from dust sensor and potentiometer value calculate motor value
  * https://www.desmos.com/calculator/5439cjbsf8
  */
void calculateMotorValue() {
  float p = map(valuePoti, 0, 1023, 200, 800) / 1000.0f; // map potentiometer to 0.2 -> 0.8
  float k = 1/p - 1;
  float b = min(valuePm25, 500.0f) / 500.0f; // convert sensor value to 0 -> 1 (mapping 0 to 0, 250 to 1)
  valueMotorDst = pow(b, k) * 1023;
  // increment motor value in small steps to get smooth increase of motor power
  if (valueMotorDst > valueMotorCur) {
    valueMotorCur = min(valueMotorCur + min(3, 1 + ((valueMotorDst - valueMotorCur) >> 5)), valueMotorDst);
  } else if (valueMotorDst < valueMotorCur) {
    valueMotorCur = max(valueMotorCur - min(12, 1 + ((valueMotorCur - valueMotorDst) >> 5)), valueMotorDst);
  }
}

/**
  * read a sample from the dust sensor and store into value buffer
  * @return true if the sensor value changed with this call
  */
void readSensorDust() {

  if (SENSOR_DUST.available()) {

    SENSOR_DUST.readBytes(BUFFER_SENSOR_DUST, SENSOR_DUST.available());

    int samplePm25 = int((unsigned char)(BUFFER_SENSOR_DUST[12]) << 8 | (unsigned char)(BUFFER_SENSOR_DUST[13]));
    if (!isnan(samplePm25) && samplePm25 >= 0 && samplePm25 < 500) {

      valueIndexPm25 = ++valueIndexPm25 % 10;
      // store at current position
      valueArrayPm25[valueIndexPm25] = samplePm25;

      // clone value array
      int _valueArrayPm25[10];
      for (int i = 0; i < 10; i++) {
        _valueArrayPm25[i] = valueArrayPm25[i];
      }

      // sort the cloned array
      for (int i = 0; i < 9; i++) {
        for (int j = i + 1; j < 10; j++) {
          if (_valueArrayPm25[i] > _valueArrayPm25[j]) {
            int swap = _valueArrayPm25[i];
            _valueArrayPm25[i] = _valueArrayPm25[j];
            _valueArrayPm25[j] = swap;
          }
        }
      }

      // reassign current value (dropping 2 smallest and 2 largest readings)
      valuePm25 = 0;
      for (int i = 2; i < 8; i++) {
        valuePm25 += valueArrayPm25[i];
      }
      valuePm25 = valuePm25 / 6;

    }

  }

}

/**
  * read and store temperature and humidity
  */
void readSensorDht() {
  float sampleHumidity = SENSOR_DHT.readHumidity();
  float sampleTemperature = SENSOR_DHT.readTemperature();
  if (!isnan(sampleHumidity)) {
    valueHumidity = sampleHumidity;
  }
  if (!isnan(sampleTemperature)) {
    valueTemperature = sampleTemperature;
  }
}



/**
  * pad a fixed number into a 4 character long string stored in CHAR_BUF
  */
void padSpace4(int number) {
  int noPadChars = floor(log10(number));
  String padded = STRING_PAD_BLANK_4.substring(noPadChars);
  padded += number;
  padded.toCharArray(CHAR_BUF, 32);
}

void padBrack4(String prefix, int number) {
  int noPadChars = (number == 0 ? 0 : floor(log10(number))) + prefix.length();
  String padded = prefix;
  padded += STRING_PAD_BRACK_4.substring(noPadChars);
  padded += number;
  padded.toCharArray(CHAR_BUF, 32);
}

void padFloat(float number) {
  dtostrf(number, 4, 1, CHAR_BUF);
}

void redrawDisplayLoop() {

  u8g.setFont(u8g_font_profont29);

  padSpace4(valuePm25);
  u8g.drawStr(24, DISPLAY_TEXT_A, CHAR_BUF);

  // switch to smaller font
  u8g.setFont(u8g_font_profont15);
  u8g.drawStr(95, DISPLAY_TEXT_A, "\xb5g/m\xb3");

  padFloat(valueTemperature);
  u8g.drawStr(47, DISPLAY_TEXT_B, CHAR_BUF);
  u8g.drawStr(76, DISPLAY_TEXT_B, "\xb0");
  u8g.drawStr(83, DISPLAY_TEXT_B, "C");

  padSpace4(valueHumidity);
  u8g.drawStr(89, DISPLAY_TEXT_B, CHAR_BUF);
  u8g.drawStr(119, DISPLAY_TEXT_B, "%");

  float lineWidthBase = 83.0f;

  int lineWidthA = valuePoti * lineWidthBase / 1023;
  int lineWidthB = valueMotorCur * lineWidthBase / 1023;
  int lineWidthC = valueMotorDst * lineWidthBase / 1023;

  u8g.drawFrame(45, DISPLAY_LINE_A - 4, lineWidthBase, 5);
  u8g.drawBox(45, DISPLAY_LINE_A - 4, lineWidthA, 5);
  u8g.drawFrame(45, DISPLAY_LINE_B - 4, lineWidthBase, 5);
  u8g.drawBox(45, DISPLAY_LINE_B - 4, lineWidthB, 5);
  u8g.drawFrame(45, DISPLAY_LINE_C - 4, lineWidthBase, 5);
  u8g.drawBox(45, DISPLAY_LINE_C - 4, lineWidthC, 5);

  u8g.setFont(u8g_font_micro);

  padBrack4("GAIN", valuePoti + 1);
  u8g.drawStr(0, DISPLAY_LINE_A + 1, CHAR_BUF);

  padBrack4("MOTOR", valueMotorCur + 1);
  u8g.drawStr(0, DISPLAY_LINE_B + 1, CHAR_BUF);

  padBrack4("", valueMotorDst + 1);
  u8g.drawStr(0, DISPLAY_LINE_C + 1, CHAR_BUF);

  u8g.drawStr(0, 5, "PM 2.5");
  String(valueArrayPm25[valueIndexPm25]).toCharArray(CHAR_BUF, 32);
  u8g.drawStr(94, 5, CHAR_BUF);

}
